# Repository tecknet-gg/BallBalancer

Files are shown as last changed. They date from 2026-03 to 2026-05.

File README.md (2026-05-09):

# Ball-Balancer

A custom 3RRS parallel manipulator that leverages CV to locate and mainpulate a ball on a 2D planar surface.

## Features:
- Low cost hardware: By leveraging edge computing the CV processing is done on a companion computer. The onboard hardware is a low cost Pi Zero 2. Frames are served over Flask, and data is received by the hardware over UDP.
- Low latency: ~75ms between frame being served and data being received back
- Resilient CV pipeline: Able to work in high noise environments. Uses a variety of techniques and optimisations, such as static and dynamic ROIs (region of interests) to reduce frame size, novel colour based filtering, ensures target is within a pre-defined HSV range to reduce false detections, and an EMA filter to maintain simplicity whilst improving performance.
- Inverse Kinematics: A robust IK class that converts target pose vectors to 3 actuator angles. 
- PID: A PID loop to calculate pose vectors taking the three (P, I & D) paramaters into account, in order to move the ball to the centre, or any arbitrary point on the plane.
- Auto-Callibration: An IMU is sampled to get orientation data, which is then fed into a basic gradient descent algorithm in order to minimise error. Setpoints can be manually defined
- Live config updating: Instead of re-deploying the code every time a paramater is chagned, a companion script running on your laptop pushes PID config paramaters over UDP, so tuning can be done in real-time, streamlining the process.

## Building

Build instructions can be found in the BUILD.md file, and instructions for running my firmware can be found in the FIRMWARE.md file.
If I do get time, I will eventually post this on Instructables!

## Pictures

### Without PCB:



### With PCB:



### My Build:



Still some tuning needed, but the hardware totally works, and it even balances it fully sometimes :]

https://www.youtube.com/shorts/TCPpPW1j67o

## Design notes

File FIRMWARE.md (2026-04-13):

The firmware is all written in python (3.13).

## Deploying and Tuning

1. Setup the Pi Zero 2 W for SSH (the setup is a bit convoluted).
2. Create a remote interpreter using your IDE of choice (easiest in PyCharm, but VSCode obviously works too).
3. Install dependencies (check imports)
4. Deploy the code to a tmp directory on the Pi Zero 2 using SSH. 
5. Run the balancer.py script on the platform. Note the IP it starts serving the frames too.
6. Set that as the target IP on the mac.py and configupdater.py scripts.
7. Set the url to to "https://nameofyourpi.local:5000/raw_feed". Example: "https://pizero2.local:5000/raw_feed"
8. In liveconfig.json, set offsets to 0.0 for all three servos. Keep PID values as is, you can tune from there.
9. In cvconfig.json, set hsvLow to [0,0,0], hsvHigh to [255,255,255] and threshold to 0.
10. Redeploy all files.
11. Run the configupdater.py script on your computer (not the balancer). Make sure you're not using the remote interpreter.
12. Run the balancer.py script on the balancer. When the Flask route has finished initialising, run the mac.py script on your computer (lke the configupdater.py).
13. Open the route displayed by the flask intialisation script from the balancer.py script, and append "/raw_stream" to the end to view the camera stream. Similarly, open the route displayed by the the flask intialisation script from the mac.py script and append "processed" to the end to view the processed stream.
14. Redefine the static RoI (region of interest) by tweaking the vertBar and horizBar if needed. If your hardware and camera is the same, it should be fine as is.
15. Rerun the mac.py script.
16. Place a ball in frame and try to achieve a lock on the ball. Try and reduce noise in the frame to achieve this. Look at the HSV readout from the balancer.py script. Set the hsvLow and hsvHigh values in the cvconfig.py script to rougly +/- 40-50 of these values. You can be more strict with this if you like. Set the threshold percentage to ~0.6. That is how much it has to be within range to be accepted. When you have a more consistent lock, tune these values to be more strict. By the end of it, you want a threshold of 0.7 - 0.8 to prevent it from loosing the ball.
17. If you cannot achieve a lock at all, tune the parameters (dp, minDist, param1, param2, minRadius and maxRadius). I would leave dp and param 1 as is. minDist isn't too important. Make param2 lower so it accepts more eliptical shapes. minRadius and maxRadius can be made more forgiving by reducing and increasing them respectively. If you have managed to achieve lock, you might want to tune the minDist and minRadius and maxRadius in particular to be more accurate, along with param2 for circularity. I go a bit more into depth of the CV pipeline on my [blog](https://tecknet.dev/blog/cv-pipeline/) post if you'd like to know more.
18. If needed tune the dynamic RoI size in the winSize variable in mac.py. This controls how large the frame is after a lock is achieved. A larger size means more pixels to process, but more accuracy and lower likelihood of loosing the ball. A lower size reduces compute time, but if the ball is moving fast, it can loose lock.
19. With that you can start tuning the PID values. They can be found in the livceconfig.json. I won't explain how to tune PID, but its the same as any PID system would be tuned.

And with that you should be done! If you have any questions about the code, feel free to contact me at hattijeevan@gmail.com or via discord if thats your thing (tecknet.gg).

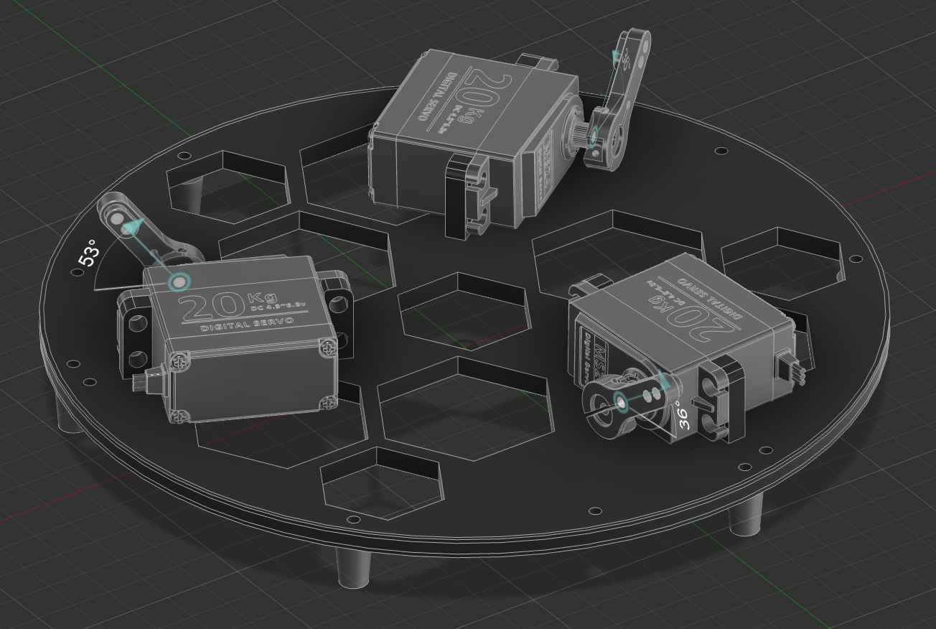
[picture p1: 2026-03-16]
images/attaching servos.png

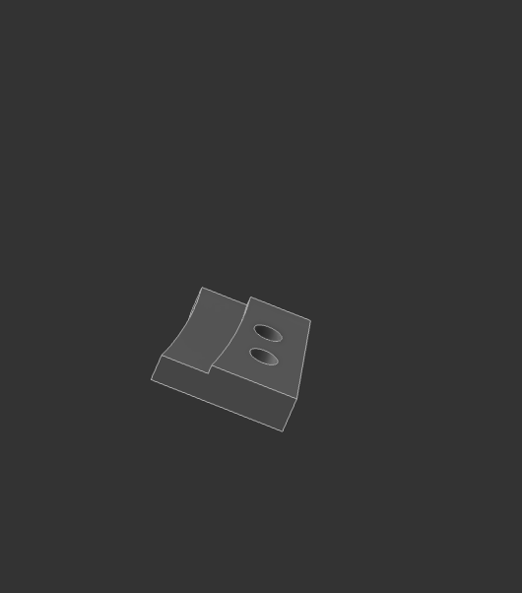
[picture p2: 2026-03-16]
images/mountclip.png

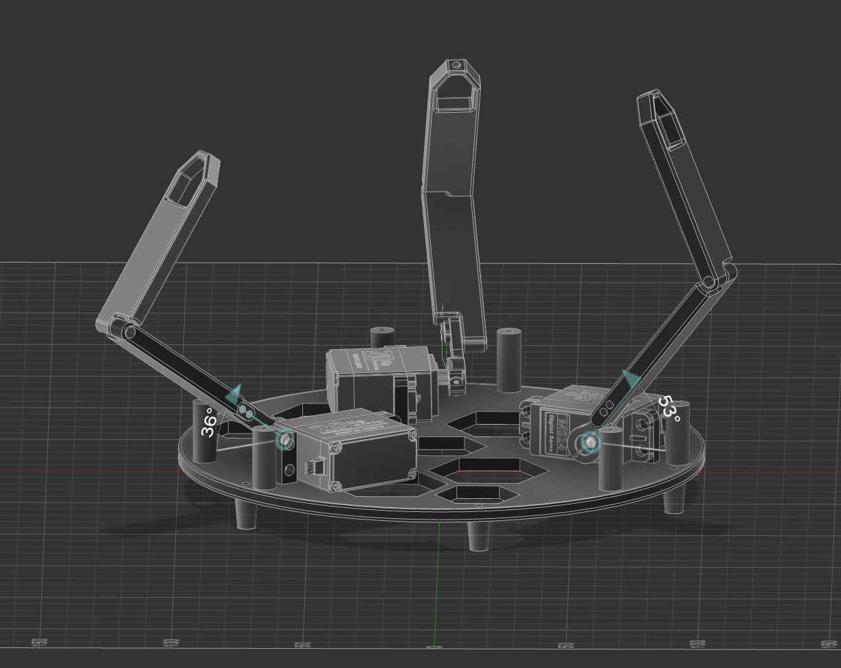
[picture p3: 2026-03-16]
images/top arm.png

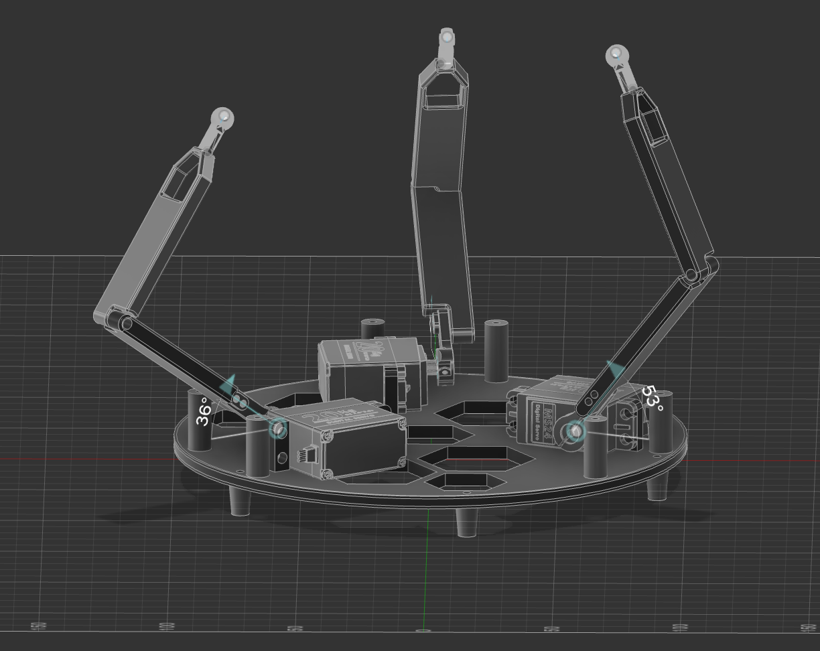
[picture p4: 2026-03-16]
images/tierod.png

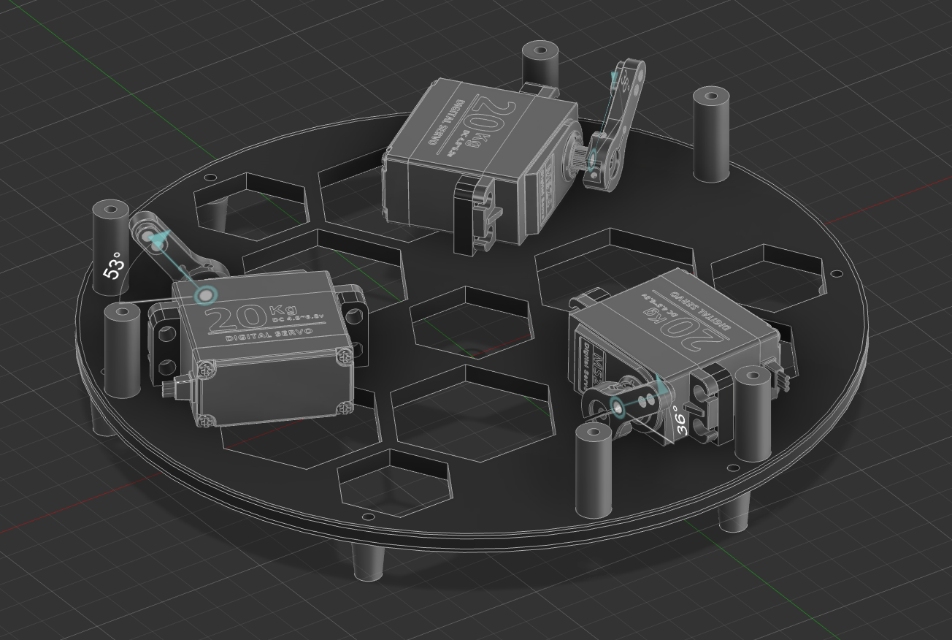
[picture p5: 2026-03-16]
images/standoffs.png

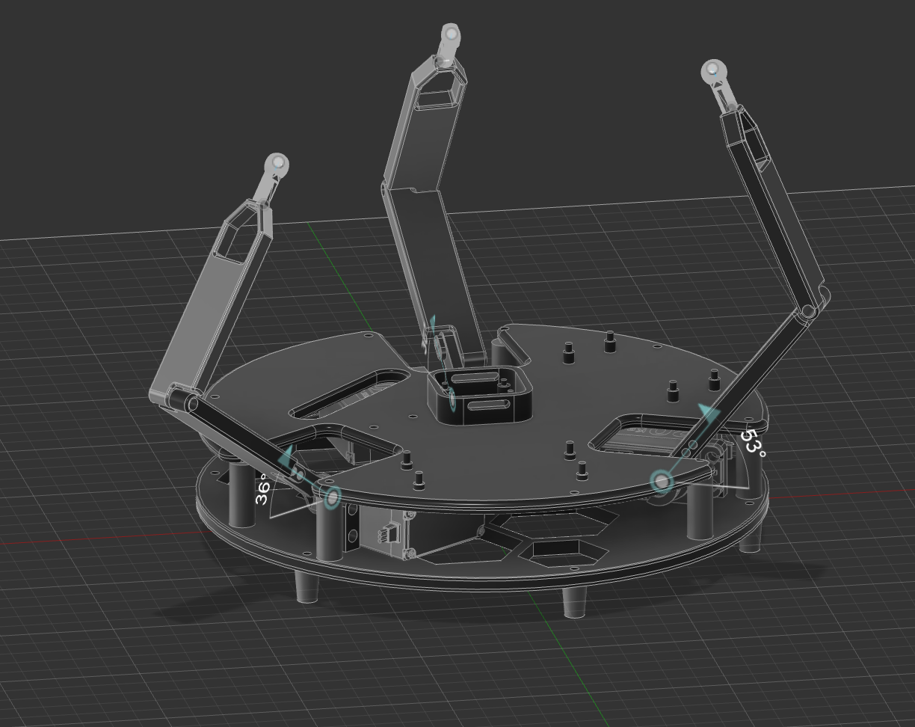
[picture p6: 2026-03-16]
images/shield.png

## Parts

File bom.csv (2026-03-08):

Component | Function | Quantity | Unit Price (£) | Total Price (£) | Source
Raspberry Pi Zero 2 W | Microcontroller | 1 | 14.15 | 14.15 | https://shop.pimoroni.com/products/raspberry-pi-zero-2-w?variant=42101934587987
Pi Camera | Camera | 1 | 7.00 | 7.00 | https://www.amazon.co.uk/dp/B0BZVP3SQW
Pi Zero Accessories | Assorted Accessories | 1 | 8.00 | 8.00 | https://shop.pimoroni.com/products/zero-adaptor-kit?variant=10462230279 https://shop.pimoroni.com/products/camera-cable-raspberry-pi-zero-edition?variant=32092803891283
Tie Rod | Joint | 10 | 0.699 | 6.99 | https://www.amazon.co.uk/dp/B0DCNGSK9S
M3/M4 Assortment | Structural | 1 | 6.64 | 6.64 | https://www.amazon.co.uk/dp/B0DG2PHL25
DS3218MG Servos | Servos | 3 | 9.997 | 29.99 | https://www.amazon.co.uk/dp/B0CY2FVZZM
PCA9685 | Servo Driver | 1 | 4.99 | 4.99 | https://www.amazon.co.uk/dp/B0BKZC1XWR
Power Supply | Power | 1 | 16.99 | 16.99 | https://tinyurl.com/2cr9nb7n
Shoulder Bolts | Pin Joints | 1 | 4.99 | 4.99 | https://www.amazon.co.uk/dp/B0FDQB24SP
PLA | Printing Material | 1 | 13.99 | 13.99 | https://www.amazon.co.uk/dp/B0CD79M1NV
20mm Acrylic Disc | Platform Disc | 1 | 3.49 | 3.49 | https://www.amazon.co.uk/dp/B0DJVB82TY
18AWG Wire | Wire | 2 | 1.45 | 2.90 | https://www.amazon.co.uk/dp/B0CZRGH4CT

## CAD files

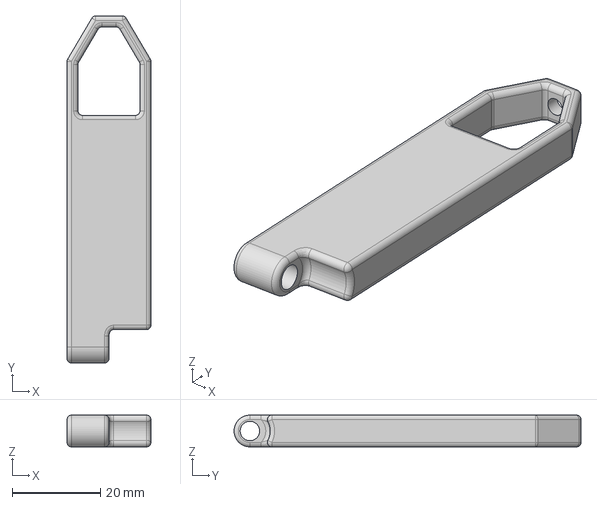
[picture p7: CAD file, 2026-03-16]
hardware/components/topleg.step
19.0 x 78.6 x 7.20 mm

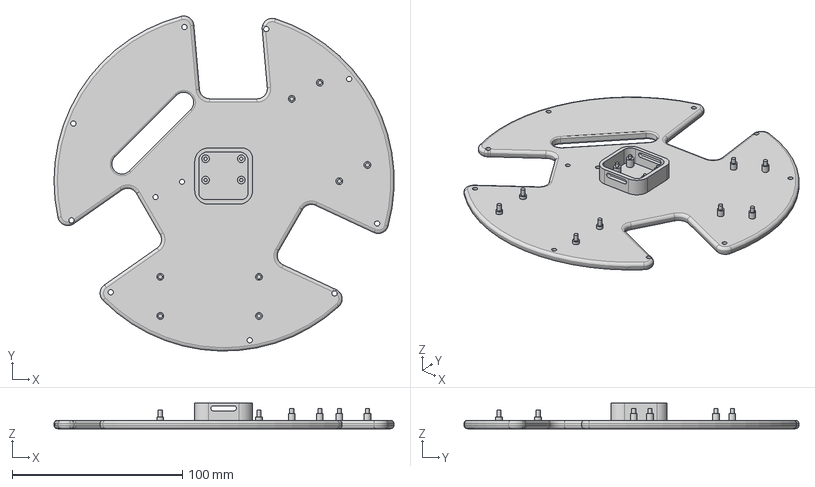
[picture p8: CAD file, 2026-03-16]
hardware/components/shield.step
199.9 x 196.9 x 15.0 mm

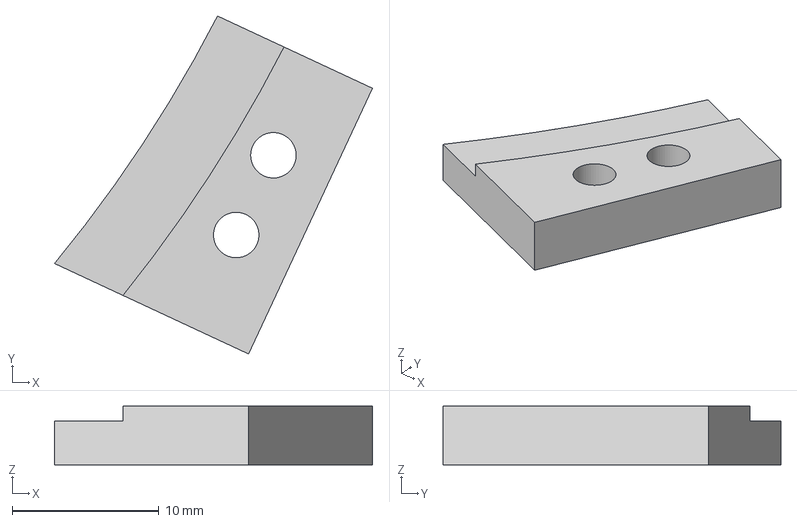
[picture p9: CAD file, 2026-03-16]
hardware/components/mountclip.step
21.7 x 23.1 x 4.00 mm

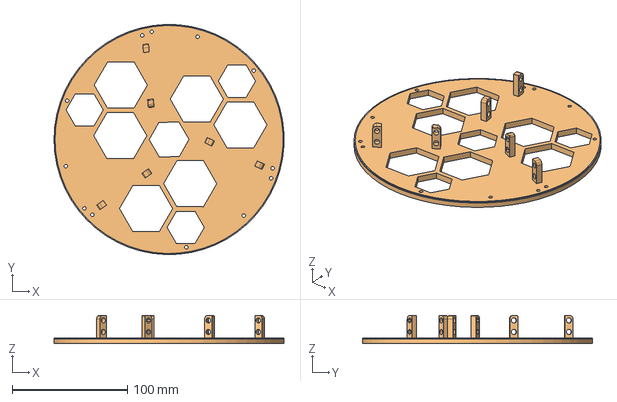
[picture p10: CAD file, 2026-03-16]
hardware/components/basefinal.step
199.8 x 199.9 x 24.6 mm

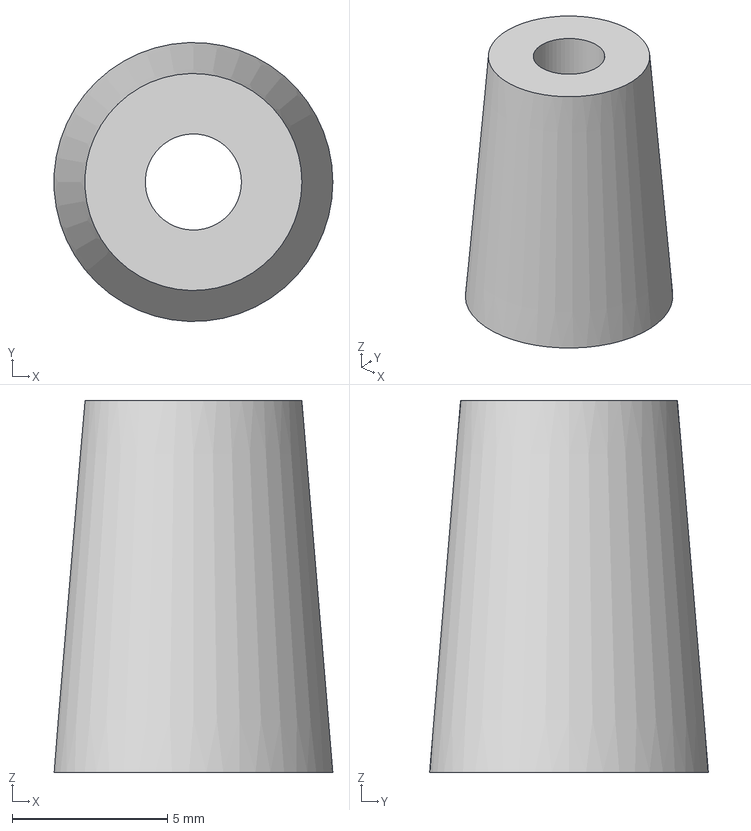
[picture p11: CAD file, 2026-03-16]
hardware/components/leg.step
8.99 x 9.00 x 12.0 mm

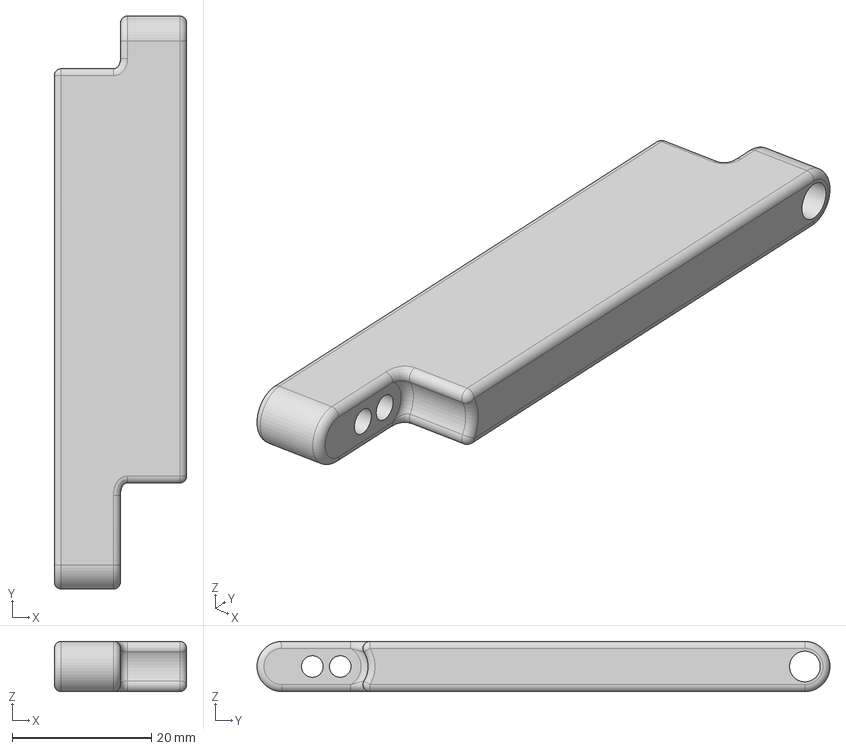
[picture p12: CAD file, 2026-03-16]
hardware/components/bottomleg.step
19.0 x 82.2 x 7.20 mm

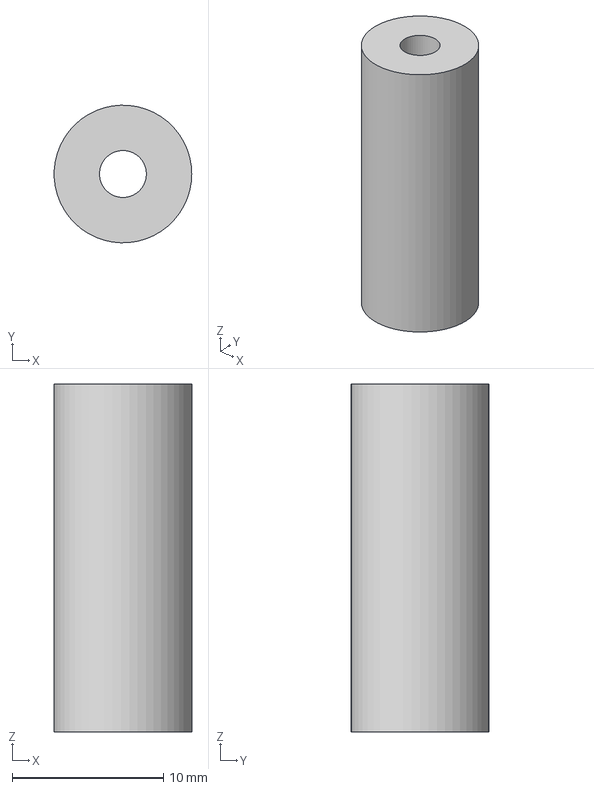
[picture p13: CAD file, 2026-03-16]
hardware/components/standoff.step
9.09 x 9.10 x 23.0 mm

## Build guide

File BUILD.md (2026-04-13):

Here's the hardware you should have on hand:

| Component | File Name | Qty | Material |
| --- | --- | --- | --- |
| Base | basefinal.step | 1 | PLA |
| Electronics Shield | shield/shieldpcb.step | 1 | PLA |
| Bottom Leg | bottomleg.step | 3 | PLA |
| Top Leg | topleg.step | 3 | PLA |
| Mount | mountfinal.step | 3 | PLA |
| Mount Clip | mountclip.step | 3 | PLA |
| Feet | leg.step | 6 | PLA |
| Standoffs | standoff.step | 6 | PLA |
| IMU Mount | IMU mount v4.step | 6 | PLA |
| Transparent Acrylic Disc | Check BOM | 1 | Acrylic  |
| Pi Zero 2 W | Check BOM | 1 | - |
| PCA9685 | Check BOM | 1 | - |
| Camera | Check BOM | 1 | - |
| Servos | Check BOM | 3 | - |
| Wires | Check BOM | - | - |
| PCB (optional) | Check pcb folder | 1 | - |
| DC Barrel Jack | Check BOM | 1 | - |
| Assorted M3 Hardware | Check BOM | - | - |
| Tie Rods | Check BOM | 3 | - |
| Shoulder Bolts | Check BOM | 3 | - |

## PCB Prep

If you decide to use the PCB, just mount the headers of the Pi Zero 2 on the underside of it, and for the PCA9685, desolder the stock headers, and replace with standard straight headers to mount to the PCB. There are screw holes too if you want to mount it with bolts, but its not needed. All fab files can be found in the pcb folder.

## Assembly

Mount the 6 feet on the circumference of the base using an M3 bolt. Apply hot glue to the underside of all 6 feet to act as a grip. Ensure you don't place them on the holes reserved for the standoffs.





Then mount and secure the three servos M3 bolts and nuts.



Attach all 6 standoffs to the remaining holes on the base:



Mount the servo horn, and attach the bottom leg to the servo horn using 2 M3 bolts/leg. You can callibrate later, but I would recommend setting all servos to 0 before using an Arduino or something, and then attach the horns.



Attach the three tops legs using a shoulder bolt, and a lock nut (two standard M3 nuts work too).



You can then put the shield onto the standoffs, with the corresponding hardware, be that the electronics as is, or with the PCB. Both go on the same.



Affix three tie rods to the top of each three legs.



Then mount the three mounts onto. Thread a bolt through it, then a nut, then feed it through the tie rod, then another nut, and out the other end of the mount, then tighten with a lock nut on the other end. It should go, bolt -> hole 1 of the mount -> nut -> tie rod -> nut -> hole 2 of the mount -> lock nut.

image

Then mount the platform onto the groove. Place the 3 mount clips upon their correspodning holes, and tighten. Et voila you should be done!



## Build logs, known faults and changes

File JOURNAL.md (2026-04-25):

And thats the journal! I am done with the project for now. There is minimal tuning left to do, but I will move onto other projects for now, and come back to this in the summer. 
For full transparecny, this was copied from the Stasis YSWS. My design was approved, but I didn't submit it to the final build approval, so I didn't use any of their funds in any way.
I didn't use Hackatime for firmware, since I started the project before Stasis had Hackatime integration, I cleared this with the staff before continuing at Stasis. I hope thats fine with Horizons.

I'm not entirely sure how Horizon calculates the hours spent. The hours I logged on Stasis are 46.3h. Thanks for reading!

# April 13th 2026 - 0.5h

So I started with the initial tuning of the platform, and I've gotten it to a point where it can move a ball to what is vaguely the centre of the platform. 

I'll finish tuning later this week. Besides that I updated the GitHub with all the final scripts and the FIRMWARE.md file that documents deploying and setting up the code. Just have to write-up the build instructions.



# April 4th 2026 - 0.75h

Spent some time integrating everything into the main class for the Balancer.

Here's everything that I've added:

A basic wrapper for the IK class:



And the main balance function (the setup then the main loop it enters):




Some of the values are hard coded as I just noticed, I'll change that eventually.

# April 4th 2026 - 2h

I implemented a basic PID class with the bog standard stuff. Its a bit verbose, but it simpler to use as a standalone unit I suppose:



I also added a very simple config updating script that pushes new config values over UDP to the balancer:



The reason I did that was because the current system works by plugging my balancer into a 6V power supply, then connecting the Pi Zero 2 to my laptop using USB Gadget mode, and controlling the Pi Zero 2 using SSH. So if I were to let the PID values live on the script that gets uploaded, I would have to re-deploy and re-initiate the entire thing, which takes a solid minute. Doing that for ever small PID change is pretty stupid, so I wrote some boilerplate code to listen for new PID values over UDP and update that live. 

I didn't mention this in yesterday's CV session, but this was mainly inspired by a similar solution I had for the CV loop, I had a simple cvconfig.json with all my HSV values, that I can tweak during run-time instead of changing a hard coded value and re-running the entire CV script.



Now all thats really left to do is integrate all this into the main Balancer class, and start tuning!

# April 4th 2026 - 4.5h

And we are done! This session was me writing up a nice concrete CV pipeline that worked well in a variety of lighting. I don't have the snippets of code as I wrote it, so I can't show you the development process, but in words, it was mainly messing around with Blurring, the detection alg (hough or contour), the paramaters, velcoity calculation and interpolation, colour filtering and some more stuff that I'll get into. I did mess around with the networking code a bit too, but nothing major was changed, it was already reliable enough as is.

Anyways, here's the loop explained!



Starting with some nice old globals. Most of them are self explanatory, the only weird one are emaCenter, which I'll get to later when I talk abotu EMA (estimated mean average). isLocked is a flag to see if the ball is locked. lastRawCenter, i don't know why I named it as such, but thats the last center for the ball we deteceted.



Some more globals here, I accidentally had them somewhere else in the preamble.

This is a neat little static RoI (region of interest). It basically defines a portion of my screen that the detector should be interested in. That was mainly because my frame had some other stuff that wasn't the platform in frame naturally.



Then we load some config data, namely the colour filter. 

It loads the necessary array, and also has a default fallback in case its missing. The threshold is how much to trust that range.



Then we actually define the mask for the RoI using rectangles:



Then we have the code for the actual RoI to be implemented



This runs when there is a lock, and the lastCenter is not none. It defines a small square around the last centre to further reduce the processing space. I called this the dynamic RoI. The bitwise and is then applied with the static and dynamic RoIs to come up with the final RoI, and that is the frame we will then process.

Here's somes standard prepcoessing:



Just grayscaling and blurring things up.

We then apply the Hough Transform, which I landed on. Its as simple as this:



I also flipped the detection flag before going into the selection process for my ideal circle.

Then we have some more novel filtering:



We extract the circle data, and then start doing some swatching on the central pixels to find the HSV values of that. Its called the orangePercent, because my blue ping pong ball shows up as orange on the NoIR camera I have instlaled right now.

Then for some pretty standard velocity calculations:



We ignore those that are moving to little by setting it to zero to filter out the raw noise. I'm not completely happy with how well tuned it is, but its something that can be improved if the need be.

Now for the filter EMA for those of you unaware is just a noise filtering thingy. Estimated Mean Average, in simpler words you define a contant that tells it how much to trust new data compared to old data. Basically? Its a bit more nuanced, and theres some math, but you shoudl google it if you want to know more. It was either that or a Kalman filter, but a Kalman filter was not something I could be bothered learning, and probably overkill too, so here we are!



Pretty straightforward impleentation.

We then just put all the data in a packet, give it a kiss goodbye, and send it off and hope and pray we're not lying to our hardware :]



Anyways here are some final annotations we put on the frame, before neatly serving this via flask too so we can oogle at it while it does its thing.



Most of the routing code is the same as you saw in the earlier networking software, so I won't bother explaining that again. But here we are! Very exciting :]

Just got PID implementing, I've already done most of the unit and integration testing, so we can just implement PID, tune it and call it a day!

# April 2nd 2026 - 1.4h

For previous sessions, I've been manually setting offsets using my phone as a spirit level, but alas, we suffer no longer. I introduce - THE AUTO CALLIBRATRON 3000.

heh. Anyways its a really janky implementation. It just uses the IMU to get pitch and rol readings, and slowly approaches them by updating the offsets and gives up when its close enough :]. I had some trouble where the 0 readings of the IMU were actually kinda slanted, and I didn't want to fix that, so adding the buffer gets a good result since it stops about ~20-30 off, and that is much more flat that going to 0,0. Fun!





# April 1st 2026 - 4h

This was... painful. Mainly because I absolutely suck at the maths I need for it. Its slightly above what I've learnt at school, but I managed to figure it out with a bit of brute force, and hand holding from the great [George Yuanji Wang](https://www.george-yuanji-wang.xyz/blog/3rrs).













After deriving the equations, it was just a matter of translating that to code, which isn't the most horrible.

I started writing up the class. The init just defines the hardware (arm lengths, platform radius etc)



The goal is for it to generate the motor angles from any given roll and pitch angle. Using the pitch and roll, I calculate the normal vector of the platform when the ball balancer is in the correct position.

With the pose vector, I then solve for coordinates of the nodes connecting the arms to the top platform. With the nodes in our local coordinate system established, you can then convert them to elbow angles, which are the angles between the top and bottom arm. Et voila! You have your motor angles. Took a lot of testing to make sure the angles it was spitting out was right, and a bit of brain wacking to realise which arm is which on my actual build. But in the end it does work! I tested it out using a loop in the main func that lets me define any pitch and roll value, and by blue-tacking a nut onto the platform to act as the normal vector so I could manually verify. 

As long as this was, it was pretty fun to work on! I'll work on auto callibration next to use the IMU. 

Heres code screenshots, I forgot to add them:






# April 1st 2026 - 3.3h

Basically the Ball Balancer's on board Pi Zero 2, while it can run full Linux, doesn't have enough compute power to viably run a CV algorithm in real time. To get past this, I'll just use the Pi Zero to stream frames over Flask to my computer, have that process the frame, and generate coordinates, and send that back to the balancer and run the PID on before moving the ball. The roundtrip latency should be made up for by the much much faster compute times my computer can offer over the Pi Zero, or even a more powerful Pi 4 or 5. 

I had to pour over the Flask Documentation for a bit to get the hang of things (and not to mention the painful SSH setup of the Pi Zero (legit took 3 hours that I won't try and count but man is that painful)). After skimming that and some documentation on the actual camera, I was done with the networking code:



I then setup the listener script on my Mac to listen for frames and stream processed frames back to the Balancer. I just used my old CV alg for the time being to get networking working:





I used some cool little lock based things so I could multithread the listening processing and streaming of data :]. Totally didn't need to but yes.


It works for the most part right now, and some small tweaks and we should be good to roll. Also I used UDP for the coordinate streaming. I kind realised Flask might be a bit slow, so I started switching halway through, then reaslied that using pure UDP for the frames would be painful, so I'm sticking with Flask, unless latency becmomes a bottleneck.

# March 30th 2026 - 3.5h

Finally started building out the platform! Used some of the old parts that I had lying aroudn as I got the newer ones printing:



Once the new parts came off the printer, I started assembling using those instead:



I then started wiring and testing the elctronics using an arduino I had lying around for now instead of the Pi Zero 2 W to keep things simple for the time being:



I wrote some cheap and dirty firmware to give each arm a little jiggle around to make sure everything was sound, and it was! Did have a bit of back and forth with my printer since some of my slicer settings were a bit shady, but I had eveyrthing printed out pretty quickly.

After testing the wiring with my Arduino, I grabbed my Pi Zero and chucked that in, along with the camera. The camera enclosure is kinda annoying, which in hindsight I saw coming. I did change it in the shield for the PCB, but I probably wont use a PCB since there isn't much point anymore. I tried chipping away the plastic for a bit instead of reprinting, but in the end I just routed the CSI cable over the enclosure bit. 

Finally when the IMU mount parts came of the printbed, I wired up my IMU and mounted it to the top platoform. And with that, I'm done building. Time to go refine my firmware now. 



# March 22nd 2026 - 0.1h

Added all the new files to the repository (the gerber and schematics) as well as the new shield. Added instructions on how to use to assemble it with or without the PCB. And modified the BOM by getting an estimate from JLCPCB







# March 22nd 2026 - 0.4h

Pretty much just what the title says. I redid the mounting posts on the top shield to accomodate the PCB. I then just imported the .step for the actual PCB, and assembled it again, and re-placed the electronics, since I couldn't be asked to link them into the actual KiCAD render.



Looks pretty cool if you ask me :]



Just gotta modify the BOM, add the new files to the GitHub, and ammend the build instructions and we should be able to re-submit for review :]

# March 22nd 2026 - 0.5h

Just polished the layout, I realised the pin for the V+ and GND was on the wrong side, so I'd have to cross wires over to get the screw terminal. Literally as I write this, I just realised I can just wire it up to the normal pin, instead of needing the screw terminal. I am stupid. Ok lemme go fix that...

But here's what it looked like before I go to fix it:



Ok that only took like 5 minutes to fix. The new bit of the schematic:



The physical PCB of course looks much the same. I'ma go ahead and export the .step and remodel the shield.

# March 21st 2026 - 2.5h

Layed out the schematic really quickly, wasn't much to that, and imported and assigned all the necessary footrpints:



After a quick google, I found out that to get the outline of my shield, I just needed to make a new sketch, project the geometry and export the .dxf, which I did pretty painlessly. I took that, and imported it into KiCad and started laying out my components:



I plopped my compoenents down where they needed to be, and spent some time defining the shape of the actual PCB:



Finished the wiring too:



Should be done with this PCB for the most part. Just gotta add some cool silkscreen stuff that I'll do tommorow I suppose. Also gotta tweak the mounting holes on the shield to accomadate the PCB.

# March 20th 2026 - 2h

Added a mount on the platfor to clip on an IMU that I had lying around. It will be used to help with auto callibrating the platform using a gradient descent algorithm. 

The clip design is pretty basic in and of its self, it just sandwhiches the platform between two parts and is tightented with some M3 bolts.



I also wrote and tested some IMU firmware and then packaged that into a neat class that I can then import and use. Getting clean data was a bit finnicky, and choosing the correct sample rate took a bittle of fiddling before I was happy with where it was. It gets relatively clean data right now, but I see myself tweaking the paramaters slightly later on.

Here is the firmware:



Also here's the actual mount:



Pretty basic but it should get the job done.

# March 16th 2026 - 0.5h

Got some feedback from the reviewer, and I addressed it. I've improved the GitHub repo to add some preliminary build instructions. Along with that, I also uploaded the individual component STEP files to make printing out the compoenents simpler. 



Also with the wiring diagram, there was one before, but I suppose it was hidden in the depths of the repo, so I've attached it to the readme as well. Hopefully that should be enough to get this approved!



# March 9th 2026 - 2.5h

I was advised to also develop firmware for the Camera and CV before submitting it for design review, so here we are!

The code is very much untested, and I fully intend on rewriting it from scratch, but I might as well take this opportunity to familiarlise myself with OpenCV. 

I read the documentation for a bit, and and once I was somewhat familiar with it, I started looking at ball detection tutorials (https://www.youtube.com/watch?v=RaCwLrKuS1w 10/10 would recommend), and implemented this follwing the tutorial into my class, along with some camera logic. I also implemented the Camera class. Still very barebones, and I need to figure out networking, but it should (in theory) be able to display a video feed, and detect a ball. I set up some basic end points for getting ball speed and location which can then be called by the PID loop when needed. Again most of this WILL be reworked later.

I also did some intensive research into CV itself, and two popular algorithms, the Hough Transform and Contour detection. To get even more familiar with this, I implemented the former myself in python! 

Here are some pictures of the pipeline:









Heres the result on a random picture I threw together in Canva (this was Hough transform). I also did some research into Contour detection, but didn't get round to impleenting that myself. 

I also found this cool picture of how the accumulator looks:



I tried really to implement this myself, but didn't get very far. Its something I want to revisit in my own time for sure though!

(Note: time spent implementing the algorithms was not included, but I thought it was fun to mention!)

Back to the actual firmware:

I'm using the Hough Transform right now in the code, but I'm still very much on the fence on whether I shoudl use this or the Contour detection. Contour detection is a fair amount faster, but implementing it isn't as easy, and either way, performance isn't really a bottleneck since I'm computing on my laptop. Right now I'm swaying towards Hough, but that might change later. 





Code will be uploaded to GitHub shortly (once I figure out how to rebase my repo)!

# March 8th 2026 - 2h

And we're done! Finished assembling the model in CAD, and spent a long long time getting all the joints to play nice. The top spherical joint was particularly painful, and after trying like 3 times, I even revereted to the old mount I had on the the very first design. Somehow after importing that in and jointing it, everything was working fine. I daren't try and replace it with the actual joint, besides, ignoring the visual oddness, it should behave the same when I actual 3D print and assemble everything.





I ran a few motion studies to make sure everything was working fine, and it all checked out.

I spent another 20 minutes or so completing the GitHub repo and uploading all necessary files for the review. 



Now time to get it reviewed 🤞,

# March 7th 2026 - 1.6h

Implemented the main firmware script in python. It will be the main balancer class. Imported my servos, and isntanstiated them. Added a bunch of helper functions and set out the basic layout of the software. 



Also made a cool little flowchart so I don't forget how this is going to work :]



While I was implementing this, I also brainstormed the idea to add an IMU to the platform to have automatic callibration. Since I would have to manually callibrate it anyways, having an automatic callibration feature would really help streamline that. I will think of adding that later on, but I want to get the project as is design reviewed ASAP.

The new code has been uploaded to the github!

# March 7th 2026 - 0.25h

The wiring is pretty simple, but its a requirement for the repository to get it past the design phase, so I quickly threw toghther this in EasyEDA:



Based it off the documentation:



Not much else to say here :]

# March 7th 2026 - 0.6h

I cleaned up an overhang that I found in the base, not entirely sure how I didn't see that before, but yeah, I fixed that so it doesn't immediately snap when I try screwing my servos in.

Additionally to save some weight, and also perhaps make wiring it a bit easier later on, I added some large cutouts to the bottom.

I ended up with this cool hexagonal pattern, and I think thats the base finalised:



I also remade the mount since I wasn't a big fan of the stupid halo thing I had going on before:



I also modelled the other half that would sandwhich the platform in between them:



# March 6th 2026 - 1h

Since I now have the servos on hand (still waiting on the Pi Zero 2), I started writing the firmware to control the servos. Pretty simple stuff:

Did have to do a bit of googling to get the maths for it, and after some debugging it was working fine.



I also started refactoring this into python for the actual firmware since I will definitely be writing the code in python. I mainly just coded it in arduino c so I can verify my maths on hardware and ensure everything is working fine, and I was a bit to eager to start programming, despite not having my Pi Zero just yet.

The code in python is basically a line by line translation of the C code, but I also encapsulated it all neatly into a class so its easier to use later on.



Also added some helper functions like sweep and update offset to streamline the code later on. The code will be up on the project github once I get to that :].

# March 6th 2026 - 2h

Finished the final main compoenent of the platform, and only have to make the assembly now.

I started the session by scouting out the CAD files for the electronics I would be using. At this stage, I've decided not to make my own custom PCB for it, since there isn't much point, I'm using a PI Zero 2, and a PCA9685, and unless I want to design a breakout board for that, which I don't particularly want to do. 

Starting where all good designs start, I extruded a circle. Actually wait I projected the base, to preserve the mounting holes... then I extruded a circle. Cool!



After some deliberation, I decided to shape my cutouts like this:



I layed out the electronics mentally, and then added a slot for the wiring of the servos, and the rounded everything off.



Next I pulled up the datasheet for my camera, and started adding the holes for the board to sit on.



I designed a little enclosure kind of thing around the camera:



Now I pretty much just added mounting holes for the PCA9865 board, and the Pi Zero 2:



A few more holes for the zip ties for cable management that I will totally get around to, and we're done!

With that modelled, I started placing in the compoenents to get a vague idea of how it would look. I will finish the fully jointed and articulatable model tommorow, and with that I think we can call the design phase (at least the initial design phase finished). Just got to write some firmware for the servos (already ordered the parts), and then we can submit it to get reviewed :].

Heres the final electronics shield:


# March 6th 2026 - 1.25h

I spent a bit of time at the start of the session brainstoriming mounting mechanisms for my platform. I didn't have the necessary tools at home to drill through the acrylic disc, so I ended up with a mount that sandwhiches the platoform between itself and another piece using and M3 screw and a nut. Pretty simple.

For the actual design of the mount, I thought I'd try out a sort of halo shaped thing. The three mounting locations would be equall spaced apart, and attached with a ring on the outer edge. The main reason I thought of making this was that it makes tuning a bit easier since it physically prevents the ball from falling off the platform. I don't think I'll keep it for the final design, but since I'd already modelled it, I suppose we're keeping it for now.



With all the core compoenents modelled again, I started with the assembly of the actual platform in CAD. I tried to be a bit more meticulous with my constraining, but I don't think everything magically fixed itself just yet.



So for the actual hardware it seems that I only need to model the shield, and perhaps do some weight optimisation for the base by adding some cutouts.

# March 5th 2026 - 2h

With the maths for the arms decided earlier, I started redesigning the entire platform. I wasn't happy with the old base, so after deliberating for a bit, I decided to stand the entire platform off the floor using some feet.

I decided to keep the old radius, and extruded it to an appropriate thickness. I imported an placed one of the servos to have a reference for the mounting holes. I decided to simplify it from the old design in the end, with two standoff things instead of the whole housing thing I had going on last time. 

I also needed to decide on the placement for the mounting holes. I needed holes for both the feet and the standoffs. With a pattern decided, I replicated it using the circular pattern. And with that the new base was modelled.

I quickly modelled some feet too, just a tapering cylinder (I suppose its a frustrum). The shorter radius circle would have some hot-glue glued on to act as a grippy grip part to dampen vibrations. I think I mentioned this in a previous journal? 

Either way, it looked something like this once I was finished with that:



Now for the interesting part, the arms. At the start, I went with the same approach as before, making a yoke style joint. After messing around with that design for a bit, I realised I didn't like where I was going with it, asthetically at least. After googling around for some inspriation, I settled with the split hinge. Each arm would form half of the hinge, and the shoulder bolt going through it would attach the two halves.

Relatively quickly, I had come with this cool design for the bottom arm.



Its much simpler than any of the other arm designs I came up with, but I think its pretty elegant. 

I spent a bit more time designing and refining the top arm. Since these arms were a fair bit thicker than the other one, I couldn't just add a tie rod to the top surface or it would look very odd. I took a few approaches, extruding a cylinder from the top to be an extension of the arm going into the tie rod, and a few other such things. In the end I settled on simply tapering it up, and creating a pentagonal cutout to let me screw the tie-rod in place.

I was pretty happy with that design. 



With the arms and base done, I have to redo the mounting, or do it for the first time, since my original was just hot-glue. I'll figure that out tommorow or over the weekend.

# March 5th 2026 - 1.5h

With the occulsion issues I noted in the first iteration, I wanted to focus a session on reviewing the geometry and getting more familiar with the platform. 

The issue that I realised was that the arms when attached to the horns were too long, and so to maintain a resaonable height above the camera, they were forced inwards ("elbows in position")  In that position, the camera was being blocked. When the arms are forced to a elbows out position, the platform is too close to the camera, and so the camera's FOV isn't great enough to capture the entire platform. 

I started researching the maths behind it, and after a while of debugging my poor algebra, and getting used to the vectors, I found out that the optimal length for the arms were around 75mm. I did this by defining a target height, and expressing that in terms of the arm lengths, and the angles between the arms and the base. I forced the angle between the base and the arm to be obtuse, and the angle between the arm and the arm to be actute to fit my target position.



I also had some fun deriving the forward kinematic equations for my platform. While for the firmware, I will need to derive the inverse kinematic equations, practing with the forward ones might help later one. They are significanly easier to derive than the inverse, so I messed around with that for a bit.



With a better familiarity with my platform and its geometry, I will set out to start the second hardware iteration later tonight, or perhaps tommorow.

# March 4th 2026 - 3.5h

I started the intial 3D modelling of my 3RRS parallel manipulator. I had already picked out components in my previous log, and so I first found 3D models for the servos that I would be using (I'll add the electronics in later). 

For inspiration, I looked at a few similar projects online during the planning, so going into it, I had a vague idea of what I wanted to model it around. 

I extruded out the base, and then placed the three servos around the base on the vertexes of an equilateral triangle. I spent a bit of time fiddling around trying to get the actual actuator part of the servo onto the corner. After I had that, I created a rigid group between the three servos and the base.





With the base modelled in, I started working on the bottom leg of the manipulator. I wasn't sure what length to make it, so I settled on the arbritrary length of 90ish mm. For the actual joint, I decided to use a yoke style joint, with a shoulder bolt going through attaching it to the top arm. I also chamfered it because I thought it looked pretty cool :]. 

After that I just modelled some holes around the servo horn, and added fillets all around. I then added rigid joints between the servo horns and the arms.



The top arm was a fair amount simpler to model. I just modelled it as a cuboid, added a cutout to allow me to screw the tie rod in for the top of the second arm. After adding some fillets for good luck, I was done with that part too.





I spent a bit of time after that trying to find the exact 3D model for the tie rod that I had sourced on Amazon, but after a few minutes of searching I couldn't find one, so I decided to start 3D modelling it. Turns out, my familiarity with Fusion360 was not good enough to allow me to do that :|..





After wasting a bit of time trying to figure out how to make it smooth and stuff, I gave up, and after a bit more digging on the internet, I found a decently close model.



I then started modelling the mount attachment for the platform at the top of the second arm. I wasn't entirely sure how I would attach it. For this iteration, since I'm assuming I will be remodelling it after, I just assumed I would hot-glue it to the platform, so there are no mounting holes or anything. Its just a simple T-Shaped mount, with a yoke-y kind of cutout for the tie-rod to slot into.



With that mirrored over, I quickly modelled the actual platform and attached it to the mounts.



While messing aroudn with the joints, I realised a critical flaw in this design, the joints were "elbow in" and so it would very significantly obstruct the camera, and would mean that there wouldn't be a clear view of the platform. This wouldn't work as I would need constant view of the ball for the camera in order to detect it. When I forced the position of the arms into an "elbow out" position, the platform would be too close to the bottom, and so I doubt the camera's FOV would allow it to see the entire platform. 



I also found out my joints were pretty broken. I'm pretty new to the entire CAD thing, and most of my projects before this have been ECAD heavy, and just used normal CAD to design enclosures, I had never used joints before. I had to learn that on the fly, and I messed up somewhere, and the entire thing breaks every once in a while. I will spend some time after this reviewing my geometry and figuring out how to properly define and contraint joints.



I did also mess around with the base, but its pretty ugly anyways, so I'll redesign the whole thing.



# March 4th 2026 - 2h

I spent this session doing all the core research and making design decisions, as well as producing a BOM. The research involved deciding between what platform to use (I ended up choosing the 3RRS parallel manipulator), my choice of actuator (deliberating between servos and steppers), how the detection of the ball would work (camera vs other sensors). I then started laying out my choices for system architecture and microcontroller choices.

After I decided to use the 3RRS parallel manipulator, I spent some time getting familiar with that. With a general sense of directione established, I started hunting for parts so I could start working on the 3D model. The BOM is at the bottom of this journal.

Below you can find a project specification document I wrote. It was written for my Crest Gold Submission (A certifcate awarded in the UK). Time spent writing the journal was not included in the journal time, only time spent researching.

Also its come to my attention that the journal does seem AI generated at first glance (the headings and all that), but please do read a few paragraphs, I think its quite evident from my weird literature that it is handwritten. Thank you!

## Project  Specifications
### Abstract
The goal of the project is to design and a build a platform to test the reliability of computer vision as a suitable sensory input in a closed loop feedback system. Computer Vision requires significant hardware overhead and may be deemed less consistent than other dedicated sensors. However the flexibility and accessibility of the solution makes it an option worth investigating. The project will involve designing and building a balancing platform that utilises visual feedback to achieve stable positioning of a ball.

### 1.1 Objectives
- To design and build a 3RRS Parallel manipulator based balancing platform
- 
- 
- To integrate a camera to provide visual feedback for real time balancing
- To design and create a closed loop PID controller using the camera for input
- To refine and evaluate the performance and limitations of visual feedback in a real time closed loop system.

### 1.2 Rationale
The choice to use computer vision in this project comes from the inherent flexibility it offers compared to other approaches that are often utilised. One common alternative uses a capacitative touch screen to locate the ball. While this approach does offer a high level of reliability, it comes with hard constraints, like the difficulty of being able to find a suitably sized screen, and the fact that the code would only work with a pre-characterised ball. Not to mention the fact that the ball has to be a weighted in order to even register on the sensor in the first place. This approach clearly has its downsides, and so an alternative was sought.

Another approach I've observed is using an IR sensor array to position the ball. While this approach too offers a high level of accuracy with minimal computing overhead, the cost and complexity of implementing an array of sensors and receivers is too high.

This is reflective of many other situations where there are multiple sensors that are capable to getting the job done, but they all trade off one thing or another. This is where visual feedback comes in. It is perhaps the most important way people sense things around us. Why not utilise this with computer too? We humans are able to perform the most complex of coordination solely with our eyes. 

Many others have asked this question, and so we have seen a drastic increase in the usage of camera's as a sensor in the modern world, facial recognition being one of the most prominent examples. However one area which is still yet to be explored to its fullest, is the application of computer vision in real time, closed loop feedback systems. The reasons are primarily to do with unreliability of algorithms in detecting and characterising its targets, coupled with the high computational overhead that it poses. 

Ultimately, this project serves to explore and push the limits of computer vision as a control input. I hope to attain a better understanding of its abilities and disadvantages that will be clear during the process of this project.

### 1.3 Requirements
#### Functional Requirements
- Full addressable 3RRS platform or equivalent
- Smooth control using PID (eliminate jittering)
- Minimal mechanical backlash
- (optional) Use PCB to clean up wiring
#### Performance Requirements
- Maintain the position of the ball within $\pm5mm$ of the centre (or any arbitrary point)
- Camera processing at 12fps minimum
- Roundtrip latency of 150ms maximum
- Operate with significant disturbances applied to the ball (to be defined later)

### 1.4 Deliverables
- 3D manipulatable platform 
- Establish camera feed
- Identify ball using Computer Vision Algorithm
- Derive inverse kinematic equations
- Implement PID loop
- Integration

### 1.5 Budget
At this stage it is hard to define a set budget, as system architecture, and final component list are not finalised yet. From previous project experience, I would estimate a budget of ~£80 on the lower end. The main costs will be the 3 servos motors, the microcontroller and miscellaneous hardware (nuts, tie rods, DC/DC buck converters etc), PLA for printing parts and the microcontroller we end up choosing. Other variable costs could include PCBs if I decide to design and fabricate them to clean up the wiring of the system.

Costs will be estimated more accurately at a later stage of the this log. Cost optimisations will be done in the hardware phase and a final cost estimate will be available by the start of the Initial Fabrication stage.

### 1.6 Proposed Timeline
##### Planning Phase
Includes drafting project specifications, and preliminary deign documents outlining systems and justifying choices. Creating the initial parts list and sourcing components. 

##### Hardware Design 
Modelling the first iteration of the project in Fusion 360, as well as creating the initial schematics for the electronics.

##### Initial Fabrication 
Buying all components and fabricating parts (3D printed). Assemble all parts to make the initial platform.

##### Testing / Iteration
Test the hardware and electronics and identify errors. Making amends to design and re-fabricate. Iterate until hardware platform is to specification.

##### Write Computer Vision Algorithm
Establish video stream over serial or WiFi and create a computer vision algorithm to detect the position of the ball on a 2D plane.

##### Write PID loop
Use inputs of computer vision algorithm to run a PID loop to create endpoints for the stepper motors to move to. This will run independent of the hardware until outputs are validated.

##### Hardware-Software Integration and Tuning
Fully integrate the hardware and software components. Test initial integration and tune the PID variables. Adjust any other aspects of code to be better compatible with the hardware.

##### Final Testing and Evaluation
Test the final platform and evaluate its performance objectively. Compare it to similar projects that employ other sensor systems and evaluate the effectiveness of my solution.

## Hardware Design

## Broad Subsystems and Component Choices
### Platform
We need to create a platform that is manipulatable in at least 2 dimensions (x and y) in order to move the ball around on the platform by tilting it in the required direction.

This would mean the bare minimum required would be a simple platform connected to two actuators (servo or stepper motors). But this would introduce instability as two points of connection perpendicular to each other might not be enough to hold up the platform. This would require extra mechanical supports to keep it balanced. 

Instead of adding a extra redundant support, I am deciding to use a 3RRS (3 actuators with two revolute joints and one spherical joint) parallel manipulator instead. This uses three actuators instead of 2, providing greater structural stability, with no extra supports required. This also provides me the ability to move the platform in 3 Dimensions, allowing flexibility for any future features that I might want to add. However it does introduce significant mathematical complexity in terms of deriving the inverse kinematic equations necessary to control it.

#### Actuator Choice

The two main choices for actuators are Stepper Motors and Servos. Both of them are completely viable choices, but each have their own caveats.

#### Stepper Motors
Stepper motors are electromechanical devices that convert digital pulses into precise rotational movements. The provide high torque output, and have minimal backlash, meaning when idle, it can hold a significant load on the actuator. Controlling them however becomes a pain point in my application as it has no loop control, so if it misses steps in its cycle, that can be an issue. 

Extra control hardware, like the TMC2209 drivers are required.

#### Servo Motors
Servos integrate a motor and sensor for position feedback to provide accurate rotational movement. You provide the servo an angle and it will turn to that precise angle. The downsides of Servos are that in order to provide as much torque as steppers, they become more expensive. However I think this trade off is worth it as it simplifies the control significantly since only an angle is required. 

Extra control hardware, while not necessary, is recommended. I will be using the PCA9685.

#### Decision
I have decided on using Servo Motors for their ease of use. Both solutions come in at near identical price points, making it a close competition, but the simplification of output control provided by the closed loop nature of Servos makes it a more approachable choice. I will be using DS3218 Servos, rated for 20KG, with a range of 270º, providing significant overhead.

Should I later consider using steppers, the most likely choice would be the NEMA 17, which is a popular form factor for stepper motors, often seen in 3D printer. They are easily sourced, and readily available, making it ideal for this project.

### System Design
At a glance there are two broad approaches I could take in system design. I shall outline them below, whilst considering their benefits and drawbacks.

#### Fully Self Contained System
This system would include all necessary hardware onboard, and would not communicate to any external computer to achieve the goal. This would entail that the computer vision algorithm and the PID loop would have to run on the onboard computer/microcontroller.

This would result in a fully self-contained system, however it would require significant onboard computational power to handle the computer vision at a frame rate suitable for the project. The likely choice of control computer in this situation would be a Raspberry Pi, which would increase the budget by significant amount.

#### Delegation
This system would offload the bulk of the heavy computational workload to an external computer, ideally a laptop. The laptop would then run both the computer vision algorithm to locate the ball, and the PID loop. It would then send the actuator end-points over to the onboard microcontroller, which is tasked with sending signals via its GPIO. 

This method would save significantly on costs as the onboard microcontroller could theoretically be something as cheap as a Raspberry Pi Pico (~£4). Some limitations of this include increased latency, however if a wired connection is used, the latency gains from the computer vision algorithm should compensate. 

Within this architecture there exist two marginally different implementation, regarding the manner in which the camera is dealt. One approach would be to use a USB camera connected directly to the laptop. The other approach would be connecting it to the microcontroller and streaming that to the laptop for processing. The only drawback of the first approach is that it would result in another data line between the platform and the laptop. The latter approach limits the choices of microcontroller, as it needs to be easily usable with a camera. I shall explore microcontroller choices later in this section.

#### Decision
I have decided to use the latter system architecture since it more cost effective, and more performant. It is also flexible in that should I later want to containerise the system, integrating an onboard computer like the Raspberry Pi, would be relatively trivial. 

### Microcontroller
In the current state of hobbyist electronics, we are spoilt for choice when it comes to microcontrollers, with there being a mainstream and well designed microcontroller fitting the most niche of needs. Here I will consider my choices and come to a decision regarding the same.

##### Raspberry Pi Pico/2/W
The Raspberry Pi Pico is a small, cheap, and relatively performant microcontroller. Its hardware is suited to drive three servo motors, and should have no difficulty in receiving and forwarding instructions from a laptop. I have a lot of prior experience working with this particular microcontroller, and it is a strong choice, considering its incredibly low cost. 

The only downside is the difficulty in using a camera with it. It is not immediately compatible with most cameras.

Variations of it also include WiFi, allowing for flexibility in communication methods with the laptop.

##### Raspberry Pi Zero/2/W
The Pi Zero is in between the Pi Pico and the traditional Pi in terms of performance and price. It is a step up from the Pi Pico, and runs full Linux. This means it is significantly more performant that the Pi Pico, however as we realised, without our current system architecture, onboard performance isn't vital. 

The main benefit of using the Zero is that it has an onboard port for camera input. This simplifies camera processing, as the Zero can run a simple script to receive and send over the video stream to the base station.

The only real downside is that it is more expensive than the Pi Pico, but still very reasonably priced relative to its performance (~£15). This makes the Pi Zero immediately more attractive than the Pico. Stock is however a challenge to acquire in the UK due to its popularity.

#### Raspberry Pi 3/4/5
The Pi would be the go to choice if I were to build a fully contained system. It is completely capable of running a CV algorithm, a PID loop and driving the servos with no issues. For the time being, I have chosen not to use the Pi for cost saving reasons. At ~£50 for a high performance model, it would take up a significant amount of the proposed budget. 

As mentioned before, switching from the delegated system to the self contained system would be relatively trivial. In fact it would simplify a good amount of the code, as packaging and sending the data between the platform and the computer would be made redundant. Due to this, the Pi will remain as a reserve choice, for if the goals of the project were to change.

#### Other Microcontrollers
Other microcontrollers that I considered include the ESP-32, a strong contender with the Pi Pico, and Arduino systems. The ESP-32 would be most likely to replace the Pico as it is more performant, and also incredibly cost effective. Arduino's on the other hand struggle to meet the price to performance that the other options offer, and so most Arduino boards will not be considered. However during the planning of this project, Arduino was bought by Qualcomm, and they have announced the new Arduino Uno Q, which is an attractive prospect. It offers an SBC (Single Board Computer), with performance comparable to a Pi 3, and two onboard chips, a Qualcomm based chip and an STM32. At its price point of ~£40 it is still a bit too expensive to consider, but if sourced for cheaper it could provide a very good alternative to the Pis, allowing me to run it all on-platform.

#### Decision
For the time being, I have come to the conclusion that the Pi Zero 2 W is the best option. It provides easy interfacing with cameras and high level threading capabilities, all at a low cost. The first iteration of the platform will be modelled assuming the Pi Zero 2 W as the microcontroller

### Other Hardware

#### Camera
Since the microcontroller we chose is the Pi Zero 2 W, the most suitable camera would be the Raspberry Pi Camera Module 2, with an appropriate adapter ribbon cable to let it slot into the smaller port on the Pi Zero 2.

#### Servo Motor Driver
A popular option is the the PCA9685. It can support up to 16 servos, providing plenty of overhead. The main use of a driver board is since a Pi Zero cannot provide nearly enough current to drive 3 Servos at once.

#### Power Supply
A 6V 10A power supply is required for the servos. They are rated for $2A$ stall current, so in the worst case scenario, our max draw would be $3\times2A = 6A$. A 10A power supply has plenty of overhead for this scenario. The microcontroller will be powered through micro-usb. It is possible to use the main power supply to power the microcontroller, it would just require a DC-DC Buck Converter to step down the 6V to the 5V necessary. I have a few buck converters on hand, and so this change might be made, if the power supply's voltage is stable enough.

## Budgeting

## Components

| Component | Function | Quantity | Price (unit*qty) | Source |
| --- | --- | --- | --- | --- |
| Raspberry Pi Zero 2 W | Microcontroller | 1 | £14.15 | https://shop.pimoroni.com/products/raspberry-pi-zero-2-w?variant=42101934587987 |
| Pi Camera | Camera | 1 | £12 | https://shop.pimoroni.com/products/raspberry-pi-camera-module-v2?variant=19833929799 |
| Pi Zero Accessories | Assorted Accessories | 1 | £8 | https://shop.pimoroni.com/products/zero-adaptor-kit?variant=10462230279 & https://shop.pimoroni.com/products/camera-cable-raspberry-pi-zero-edition?variant=32092803891283 |
| Tie Rod | Joint | 10 | £6.99 | https://www.amazon.co.uk/dp/B0DCNGSK9S/?coliid=IMXWIUSGWOUHA&colid=3NYE67N1E05KC&psc=1 |
| M3/M4 Assortment | Strcutural | ~ | £6.64 | https://www.amazon.co.uk/dp/B0DG2PHL25/?coliid=I26YB3K78HFTZQ&colid=3NYE67N1E05KC&psc=1 |
| DS3218MG | Servos | 3 | £29.99 | https://www.amazon.co.uk/dp/B0CY2FVZZM/?coliid=I2RXC2YMY9KN9T&colid=3NYE67N1E05KC&th=1 |
| PCA9685 | Servo Driver | 1 | £4.99 | https://www.amazon.co.uk/dp/B0BKZC1XWR/?coliid=I37WT66U57CC7J&colid=3NYE67N1E05KC&psc=1 |
| Power Supply | Power | 1 | £16.99 | https://tinyurl.com/2cr9nb7n |
| Shoulder Bolts | Pin Joints | | £4.99 | https://www.amazon.co.uk/dp/B0FDQB24SP?ref=ppx_yo2ov_dt_b_fed_asin_title |
| PLA | Printing Material | 1 | £13.99 | https://www.amazon.co.uk/dp/B0CD79M1NV?ref=ppx_yo2ov_dt_b_fed_asin_title |
| 20mm Acrylic Disc | Platform Disc | 1 | £3.49 | https://www.amazon.co.uk/dp/B0DJVB82TY/?coliid=I2NBRJSN1CBSC1&colid=3NYE67N1E05KC&psc=1 |
| 18AWG Wire | Wire | 2 | £2.90 | https://www.amazon.co.uk/dp/B0CZRGH4CT/?coliid=I36BQ0C4MRSHG2&colid=3NYE67N1E05KC&psc=1 |
Total Estimate: £127.97

Notes:

Pi Zero 2 W out of stock at all major UK retailers, and Amazon resellers selling well above MSRP. Will await further stock.



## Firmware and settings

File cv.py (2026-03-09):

import threading

import cv2 as cv
import numpy as np
from picamera2 import Picamera2
import cv2 as cv
import numpy as np
import math
import time


prevCircle = None

class BallTracker:
    def __init__(self,camecoordinates,lock): #provide coordinates and lock for reading variable safely (will be multithreaded)
        self.coordinates = None
        self.cam.configure(self.cam.create_preview_configuration(main={"size": (640, 480)}))
        self.cam.start()
        self.prevCircle = None

        time.sleep(1)
    def locateBall(self, frame): #to call from PID loop
        return self.coordinates,frame
    def dist(self,x1,x2,y1,y2):
        return math.sqrt((x2-x1)**2 + (y2-y1)**2)
    def findCircle(self,frame):
        pass

    def display(self):
        while True:
            frame = self.cam.capture_array()

            greyFrame = cv.cvtColor(frame, cv.COLOR_BGR2GRAY)
            blurFrame = cv.GaussianBlur(greyFrame, (19, 19), 0)
            circles = cv.HoughCircles(blurFrame, cv.HOUGH_GRADIENT, dp=1.2, param1=100, minRadius=50, maxRadius=150)
            chosen = None
            if circles is not None:
                circles = np.uint16(np.around(circles))
                for circle in circles[0, :]:
                    if chosen is None:
                        chosen = circle
                    elif prevCircle is not None:
                        #pick whichever circle is closer to previous position
                        if self.dist(circle[0], circle[1], prevCircle[0], prevCircle[1]) < self.dist(chosen[0], chosen[1], prevCircle[0], prevCircle[1]):
                            chosen = circle

                if chosen is not None:
                    cv.circle(frame, (chosen[0], chosen[1]), 1, (255, 0, 0), 3)
                    cv.circle(frame, (chosen[0], chosen[1]), chosen[2], (0, 255, 0), 3)
                    prevCircle = (chosen[0], chosen[1])
            else:
                cv.putText(frame, "No ball detected", (30, 50),
                           cv.FONT_HERSHEY_SIMPLEX, 1, (0, 255, 0), 1)

            cv.imshow("Video", frame)


if __name__ == "__main__":
    coordinates = [None, None]
    lock = threading.Lock()
    tracker = BallTracker(coordinates,lock)
    tracker.display()

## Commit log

2026-03-07 added servo.ino
    basic firmware written in arduino, not used, just for hardware verification before porting to python
2026-03-07 added wiring diagram
2026-03-08 added bom.csv
    [bom.csv]
2026-03-09 camera and cv firmware
2026-03-16 added assembly instructions
    still need pictures
2026-03-16 add wiring diagram
2026-03-16 added mountclip image
2026-03-16 added individual compoenent step files
    [basefinal.step, bottomleg.step, leg.step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]
2026-03-22 create pcb folder
2026-03-22 added pcb schematic
    [ballbalancerschm.kicad_sch]
2026-03-22 Update README with custom PCB details and assembly
    Added information about the custom PCB and its assembly instructions.
2026-03-22 new pcb
2026-03-22 new pcb
    with drill holes this time...
